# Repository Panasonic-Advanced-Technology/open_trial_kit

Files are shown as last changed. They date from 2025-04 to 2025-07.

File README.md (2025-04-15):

# @mobi open_trial_kit 1.0

@mobi Open Trial Kit 1.0は、手軽にAMR/AGVの実験や研究開発に使用できる台車として設計しました。
会社から購入しやすいようにネット通販のみで入手できる部品は極力使用していません。

組み立て方法については下記の記事をご参照ください。

[@mobi Open Trial Kit 1.0]
https://qiita.com/yamamoto-kazusige/items/2093b6a97f03b2b13532

******************************************************************************
 @mobi Open Trial Kit 1.0は、パナソニック アドバンストテクノロジー株式会社が
 配布しています。
 使用している部品メーカー様にお問い合わせなさらないようにお願いします。
******************************************************************************

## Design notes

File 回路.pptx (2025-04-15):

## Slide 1

照光スイッチ

Emg

非常停止ﾎﾞﾀﾝ

FG

24V

BLV-KRD

RS485GND 22
RS485+ 23
RS485- 24

FG

0V

Batt 12V

Batt 12V

通信電源+

20

HE
リレー

通信電源-

QSTOP

21

18

15

IN-COM

24V

BLV-KRD

RS485GND 8
RS485+ 9
RS485- 10

コントローラの
RS485へ

22
23
24

B-

B+ 24V

FG

0V

充電
ｺﾈｸﾀ

通信電源+

通信電源-

20

21

IN-COM

QSTOP

18

15

コモン端子台TNC10

DCDC
24V->12V

ｵﾑﾛﾝ端子台

FG

OUT12V

コモン端子台TNC10

IN24V

PC

20LX

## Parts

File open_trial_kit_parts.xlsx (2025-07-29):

 |  |  |  |  |  |  | 価格は 2025/7 現在のものです
 | 品名 |  | メーカー | 品番・仕様 | 数量 | 発注数 | 概算価格 | 合計
 | モーター |  |  |  |  |  |  | 142180
 |  | ブラシレスモーター | オリエンタルモーター | BLMR460SHK-GFV | 2 | 2 | 21000 | 42000 | https://www.orimvexta.co.jp/shop/item/detail/00144838/
 |  | ギヤヘッド | オリエンタルモーター | GFV4G15 | 2 | 2 | 11500 | 23000 | https://www.orimvexta.co.jp/shop/item/detail/00136830/
 |  | ドライバ | オリエンタルモーター | BLVD-KRD | 2 | 2 | 32130 | 64260 | https://www.orimvexta.co.jp/shop/item/detail/00139688/
 |  | 接続ケーブル(30cm) | オリエンタルモーター | CCM003B1ABF | 2 | 2 | 2720 | 5440 | https://www.orimvexta.co.jp/shop/item/detail/00144801/
 |  | モーター取付金具 | オリエンタルモーター | SOL4M6F | 2 | 2 | 2380 | 4760 | https://www.orimvexta.co.jp/shop/item/detail/00134044/
 |  | 電源ケーブル | オリエンタルモーター | LC03D06A | 2 | 2 | 1360 | 2720 | https://www.orimvexta.co.jp/shop/item/detail/00131331/
 | 電源系 |  |  |  |  |  |  | 38520
 |  | バッテリーパック | モノタロウ | MNX4L-BS | 2 | 2 | 2498 | 4996 | https://www.monotaro.com/p/7589/7624/?t.q=MNX4L-BS
 |  | 充電器 | メルテック | MP-230 | 1 | 1 | 14980 | 14980 | https://www.monotaro.com/p/4505/0478/?t.q=MP-230
 |  | 充電コネクタ | Neutrik | NL4FX | 1 | 1 | 2172 | 2172 | https://amzn.asia/d/9i35Aej
 |  | 充電コネクタ | Neutrik | NL4MP-ST | 1 | 1 | 1600 | 1600 | https://amzn.asia/d/6iJaPEA | https://www.mouser.jp/ProductDetail/Neutrik/NL4MP-ST?qs=erV61lVMmP8w7yPIYNaFtw%3D%3D
 |  | DCDC | MEAN WELL | DDR-60G-12 24->12V 60W | 1 | 1 | 6020 | 6020 | https://www.mouser.jp/ProductDetail/MEAN-WELL/DDR-60G-12
 |  | 電圧計 | amazon |  | 1 | 1 | 695 | 695 | https://amzn.asia/d/bLz6KK5
 |  | 非常停止ボタン | IDEC | ミスミ品番：AB6E-3BV01PRH | 1 | 1 | 1540 | 1540 | https://jp.misumi-ec.com/vona2/detail/222000391908/?PNSearch=AB6E-3BV01PRH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
 |  | パワーリレー | Panasonic | HE1AN-S-DC24V | 1 | 1 | 2720 | 2720 | https://jp.misumi-ec.com/vona2/detail/222005836525/?PNSearch=HE1AN-S-DC24V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
 |  | 低電圧保護基盤 | ---- | ---- | 1 | 1 | 1636 | 1636 | https://amzn.asia/7wLcxFT
 |  | 照光押ボタンスイッチ | IDEC | AL6H-A14PG | 1 | 1 | 1698 | 1698 | https://www.monotaro.com/p/5976/9927/
 |  | スイッチガード | IDEC | AL-KH6S | 1 | 1 | 229 | 229 | https://www.monotaro.com/p/0248/4194/
 |  | DINレール | ミスミ | DNR315-200 | 1 | 1 | 234 | 234 | https://jp.misumi-ec.com/vona2/detail/110302032560/?PNSearch=DNR315-200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
 | 端子台 |  |  |  |  |  |  | 4230
 |  | コモン端子台(4個入) | パトライト | TNC10 | 1 | 1 | 2968 | 2968 | https://jp.misumi-ec.com/vona2/detail/222005625813/?HissuCode=TNC10
 |  | 信号端子台 | オムロン | XW5T-P1.5-1.2-1 | 5 | 5 | 96 | 480 | https://www.monotaro.com/p/2440/9367/
 |  | XW5T-P用 ストッパ | オムロン | XW5Z-EP6 | 2 | 2 | 54 | 108 | https://www.monotaro.com/p/2440/9254/
 |  | ショートバー | オムロン | XW5S-P1.5-2RD | 4 | 4 | 99 | 396 | https://www.monotaro.com/p/2441/2106/
 |  | ショートバー | オムロン | XW5S-P1.5-3RD | 2 | 2 | 139 | 278 | https://www.monotaro.com/p/2441/2072/
 | コントローラー |  |  |  |  |  |  | 28944
 |  | PC | N97 MINI PC |  | 1 | 1 | 28944 | 28944 | https://amzn.asia/d/bluqHM6
 | 車輪 |  |  |  |  |  |  | 51032
 |  | 駆動輪ホイール | meviy | MVTUP-APW-456-7J5B4 | 2 | 2 | 15434 | 30868 | https://meviy.misumi-ec.com/ja-jp/
 |  | 金属ワッシャ | ミスミ | FWSSA-D30-V5.5-T4 | 2 | 2 | 510 | 1020 | https://jp.misumi-ec.com/vona2/detail/110300231910/?PNSearch=FWSSA-D30-V5.5-T4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
 |  | 駆動輪ウレタン A70 | ミスミ | AXFM-D125-L30-V85-N | 2 | 2 | 5510 | 11020 | https://jp.misumi-ec.com/vona2/detail/110300272940/?PNSearch=AXFM-D125-L30-V85-N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
 |  | センターボルト | ミスミ | HXNHFFLT-SUS-M5-12 | 2 | 2 | 36 | 72 | https://jp.misumi-ec.com/vona2/detail/221005020811/?PNSearch=HXNHFFLT-SUS-M5-12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
 |  | キャスター | シシク | 緩衝キャスター SAJ-TS6-SJ-50R | 2 | 2 | 4026 | 8052 | https://jp.misumi-ec.com/vona2/detail/221000601530/?HissuCode=SAJ-TS6-SJ-50R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
 | フレーム部材 |  |  |  |  |  |  | 74933
 |  | 底板 | meviy | MVSHM-AW05001-3WF-EFSA2 | 1 | 1 | 10832 | 10832 | https://meviy.misumi-ec.com/ja-jp/
 |  | IMU固定板 | meviy | MVSHM-AW05003-3WF-T2MRD | 1 | 1 | 5842 | 5842 | https://meviy.misumi-ec.com/ja-jp/
 |  | スイッチパネル | meviy | MVSHM-AS03002-3Y5-72S4S | 1 | 1 | 9406 | 9406 | https://meviy.misumi-ec.com/ja-jp/
 |  | コネクタスペーサー（3Dプリンタ出力もOK） | meviy | MVBLK-ABN-3Y6-E6DKS | 1 | 1 | 3268 | 3268 | https://meviy.misumi-ec.com/ja-jp/
 |  | LiDARベース | meviy | MVSHM-3N03000-456-YRTZX | 1 | 1 | 2424 | 2424 | https://meviy.misumi-ec.com/ja-jp/
 |  | PCベース | meviy | MVSHM-3N03000-3Y6-M7CMU | 1 | 1 | 2527 | 2527 | https://meviy.misumi-ec.com/ja-jp/
 |  | モータースペーサ（3Dプリンタ出力もOK) | meviy | MVBLK-ABN-3Y6-U1AJ9 | 2 | 2 | 4005 | 8010 | https://meviy.misumi-ec.com/ja-jp/
 |  | モータースペーサ（3Dプリンタ出力もOK) | meviy | MVBLK-ABN-3Y6-Y89JW | 2 | 2 | 3180 | 6360 | https://meviy.misumi-ec.com/ja-jp/
 |  | キャスター取り付けプレート | ミスミ | JSHDS-SUD-A60-B60-T2-L30-G30-N8-D12.5 | 2 | 2 | 1480 | 2960 | https://jp.misumi-ec.com/vona2/detail/110302699840/?PNSearch=JSHDS-SUD-A60-B60-T2-L30-G30-N8-D12.5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
 |  | アルミフレーム2 | ミスミ | NFS5-2080-102.5-TPW | 3 | 3 | 1941 | 5823 | https://jp.misumi-ec.com/vona2/detail/110311093859/?PNSearch=NFS5-2080-102.5-TPW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
 |  | アルミフレーム3 | ミスミ | NFSL6-3060-105-RTP | 1 | 1 | 736 | 736 | https://jp.misumi-ec.com/vona2/detail/110311094849/?PNSearch=NFSL6-3060-105-RTP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
 |  | アルミフレーム4 | ミスミ | NFS6-6060-50-TPW-CW | 2 | 2 | 2310 | 4620 | https://jp.misumi-ec.com/vona2/detail/110311095569/?PNSearch=NFS6-6060-50.5-TPW-CW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
 |  | アルミフレーム5 | ミスミ | NFSL6-3030-300 | 2 | 2 | 190 | 380 | https://jp.misumi-ec.com/vona2/detail/110311092329/?PNSearch=NFSL6-3030-300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
 |  | アルミフレーム6 | ミスミ | NFSL6-3030-172 | 2 | 2 | 178 | 356 | https://jp.misumi-ec.com/vona2/detail/110311092329/?PNSearch=NFSL6-3030-172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
 |  | フレームキャップ | ミスミ | HFC6-3030-S | 4 | 4 | 178 | 712 | https://jp.misumi-ec.com/vona2/detail/110300446540/?PNSearch=HFC6-3030-S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
 |  | 低頭六角穴ボルト M5 10mm | ミスミ | CBSA5-10 | 15 | 15 | 90 | 1350 | https://jp.misumi-ec.com/vona2/detail/110302603510/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
 |  | 低頭六角穴ボルト M8 10mm | ミスミ | CBSA8-10 | 10 | 10 | 140 | 1400 | https://jp.misumi-ec.com/vona2/detail/110302603510/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
 |  | インサート M5 M8 ピッチ1.25 | --- | １０個入り | 1 | 1 | 897 | 897 | https://amzn.asia/d/d7DC6Oo
 |  | 六角穴ボルト M3 8mm | ミスミ | CBE3-8 | 7 | 10 | 58 | 580 | https://jp.misumi-ec.com/vona2/detail/110302280360/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
 |  | 皿小ねじ M3 20mm | SUNCO | CSPCSZ-STU-M3-20 | 2 | 4 | 17 | 68 | https://jp.misumi-ec.com/vona2/detail/221000547315/?PNSearch=CSPCSZ-STU-M3-20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
 |  | 六角穴ボルト M4 15mm | ミスミ | CBE4-15 | 4 | 4 | 90 | 360 | https://jp.misumi-ec.com/vona2/detail/110302280360/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
 |  | 六角穴ボルト M5 12mm | ミスミ | CBE5-12 | 28 | 28 | 59 | 1652 | https://jp.misumi-ec.com/vona2/detail/110302280360/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
 |  | 六角穴ボルト M5 25mm | ミスミ | CBE5-25 | 8 | 10 | 59 | 590 | https://jp.misumi-ec.com/vona2/detail/110302280360/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
 |  | 六角ナット M5 | ミスミ | LBNR5 | 2 | 2 | 81 | 162 | https://jp.misumi-ec.com/vona2/detail/110300250540/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
 |  | 六角ナット M12 | ミスミ | LBNR12 | 2 | 2 | 170 | 340 | https://jp.misumi-ec.com/vona2/detail/110300250540/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
 |  | 平座金 M5 | ミスミ | PWF5 | 2 | 2 | 102 | 204 | https://jp.misumi-ec.com/vona2/detail/110300252910/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
 |  | フレームナット6シリーズM5 後入れバネナット | ミスミ | HNTP6-5 | 4 | 4 | 49 | 196 | https://jp.misumi-ec.com/vona2/detail/110302611210/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
 |  | フレームナット6シリーズM5 後入れ | ミスミ | HNTA6-5 | 33 | 33 | 40 | 1320 | https://jp.misumi-ec.com/vona2/detail/110302611120/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
 |  | フレームナット5シリーズM4 バネナット | ミスミ | HNTU5-4 | 4 | 4 | 52 | 208 | https://jp.misumi-ec.com/vona2/detail/110302608140/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
 |  | 連結ブラケット6シリーズ2穴 | ミスミ | HBLFSDK6 | 2 | 2 | 241 | 482 | https://jp.misumi-ec.com/vona2/detail/110300442950/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
 |  | 連結ブラケット5シリーズ2穴 | ミスミ | HBLFSDK5 | 2 | 2 | 230 | 460 | https://jp.misumi-ec.com/vona2/detail/110300437620/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
 |  | 連結ブラケット6シリーズ直角 | ミスミ | HBLFS6 | 6 | 6 | 68 | 408 | https://jp.misumi-ec.com/vona2/detail/110300442860/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
 | 天板（無くても良い） |  |  |  |  |  |  | 10509
 |  | アルミ天版 | meviy | MVSHM-AN05000-3Y6-ANRC2 | 1 | 1 | 7635 | 7635 | https://meviy.misumi-ec.com/ja-jp/
 |  | アルミフレーム支柱 | ミスミ | NFSL6-3030-90-RTP | 3 | 3 | 500 | 1500 | https://jp.misumi-ec.com/vona2/detail/110311092329/?PNSearch=NEFS6-3030-90-RTP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
 |  | 連結ブラケット6シリーズ直角 | ミスミ | HBLFS6 | 3 | 3 | 68 | 204 | https://jp.misumi-ec.com/vona2/detail/110300442860/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
 |  | フレームナット6シリーズM5 後入れ | ミスミ | HNTA6-5 | 6 | 6 | 40 | 240 | https://jp.misumi-ec.com/vona2/detail/110302611120/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
 |  | 六角穴ボルト M5 12mm | ミスミ | CBE5-12 | 6 | 6 | 85 | 510 | https://jp.misumi-ec.com/vona2/detail/110302280360/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
 |  | 低頭六角穴ボルト M8 10mm | ミスミ | CBSA8-10 | 3 | 3 | 140 | 420 | https://jp.misumi-ec.com/vona2/detail/110302603510/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
 | 合計 |  |  |  |  |  |  | 350348
その他調達部材(センサー例)
 | センサー
 |  | 2D LiDAR | 北陽電機 | UST-20LX | 1 | 1
 |  | IMU | WitMotion | HWT901B | 1 | 1 |  |  | https://amzn.asia/d/g8VlMhx

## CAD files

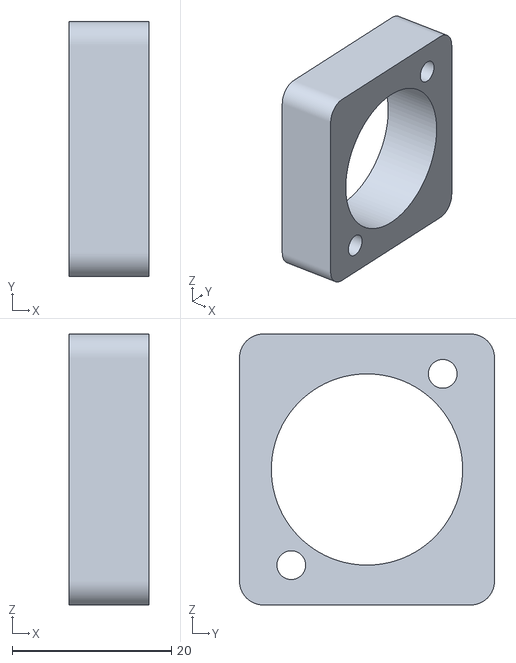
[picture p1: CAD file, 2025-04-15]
CAD/3Dプリンタ/コネクタースペーサ.stl
10.0 x 32.0 x 34.0

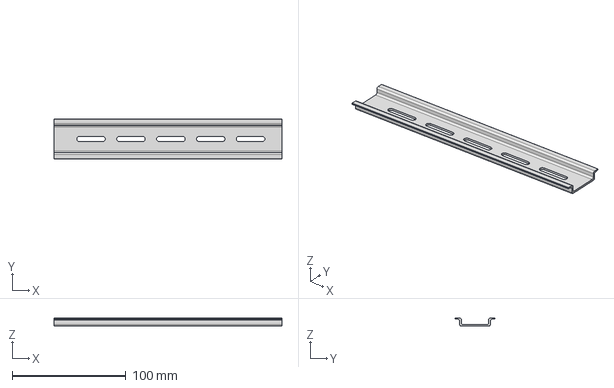
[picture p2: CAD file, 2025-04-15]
CAD/ダウンロードCADデータ/DNR274-200.stp
200.0 x 35.0 x 7.30 mm

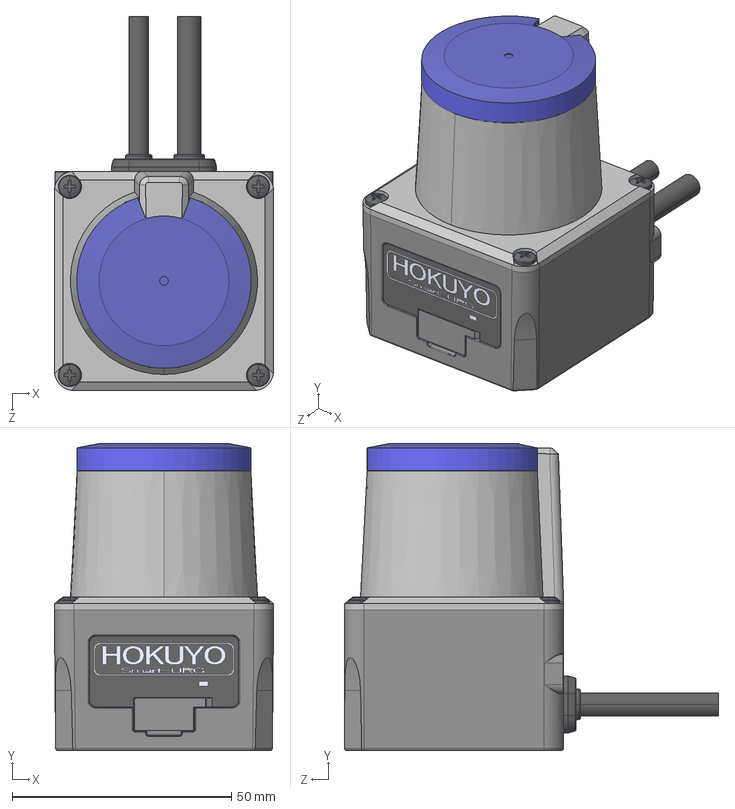
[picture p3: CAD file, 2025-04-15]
CAD/ダウンロードCADデータ/UST-10_20LX_3DCAD/UST-10_20LX.STEP
50.0 x 70.0 x 85.3 mm

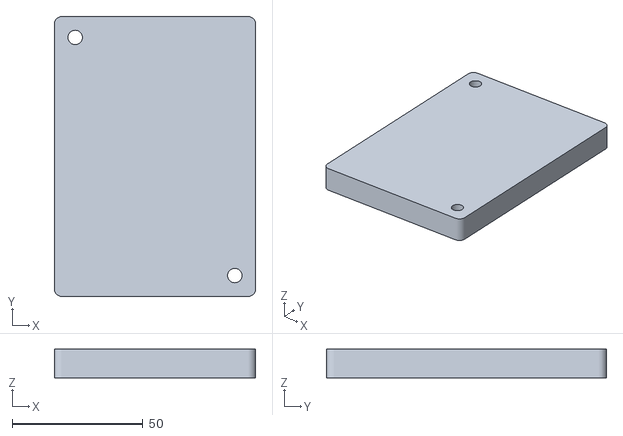
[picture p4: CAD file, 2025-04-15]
CAD/3Dプリンタ/PCベース.stl
77.0 x 107.0 x 11.0

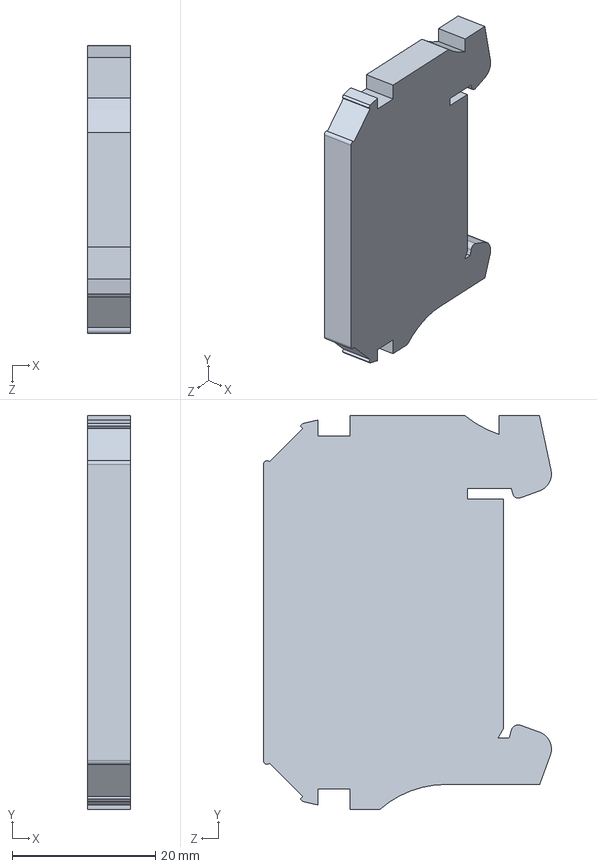
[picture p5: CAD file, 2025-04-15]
CAD/ダウンロードCADデータ/XW5Z_EP6.step
6.00 x 55.0 x 40.2 mm

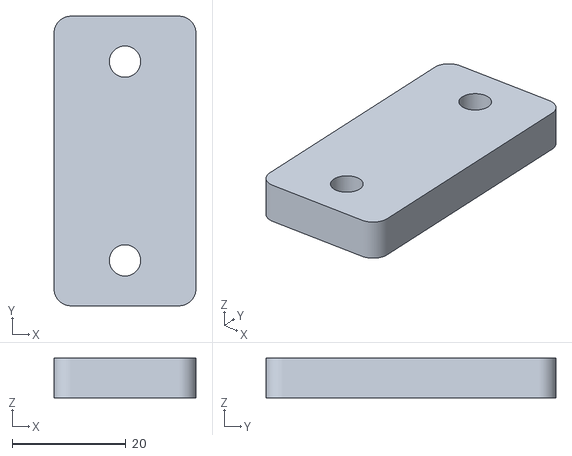
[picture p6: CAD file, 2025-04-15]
CAD/3Dプリンタ/モータースペーサー.stl
25.0 x 51.0 x 7.00

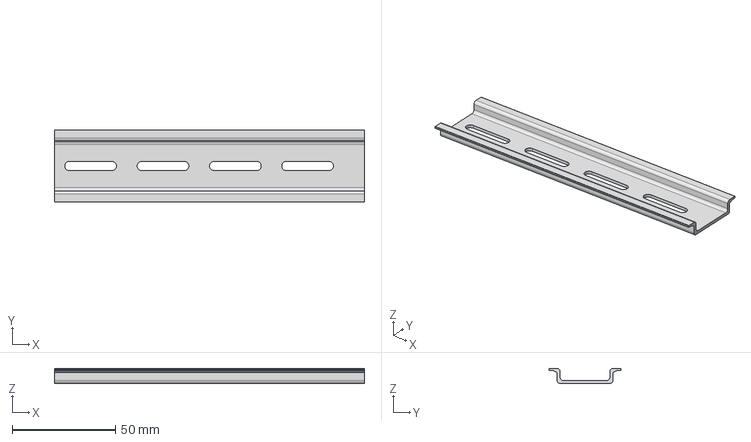
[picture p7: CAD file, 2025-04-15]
CAD/ダウンロードCADデータ/DNR274-150.stp
150.0 x 35.0 x 7.30 mm

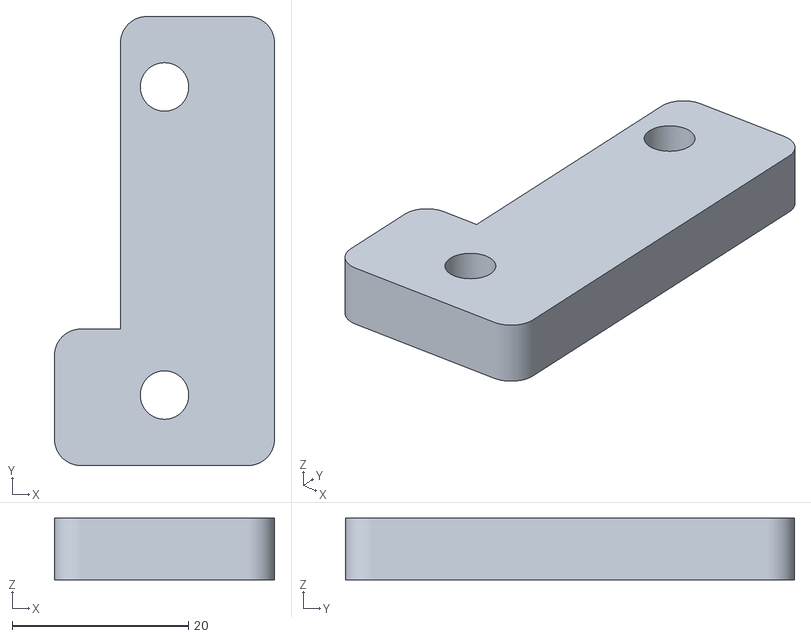
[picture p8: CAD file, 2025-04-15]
CAD/3Dプリンタ/モータースペーサー2.stl
25.0 x 51.0 x 7.00

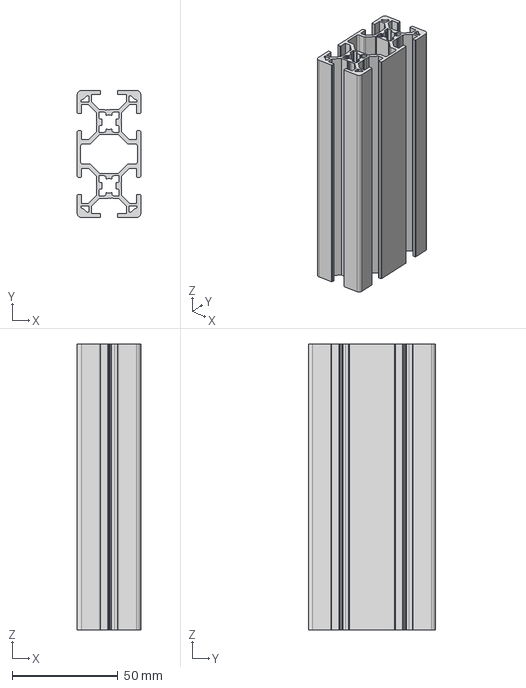
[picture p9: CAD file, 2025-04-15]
CAD/ダウンロードCADデータ/NEFS6-3060-135.stp
30.0 x 60.0 x 135.0 mm

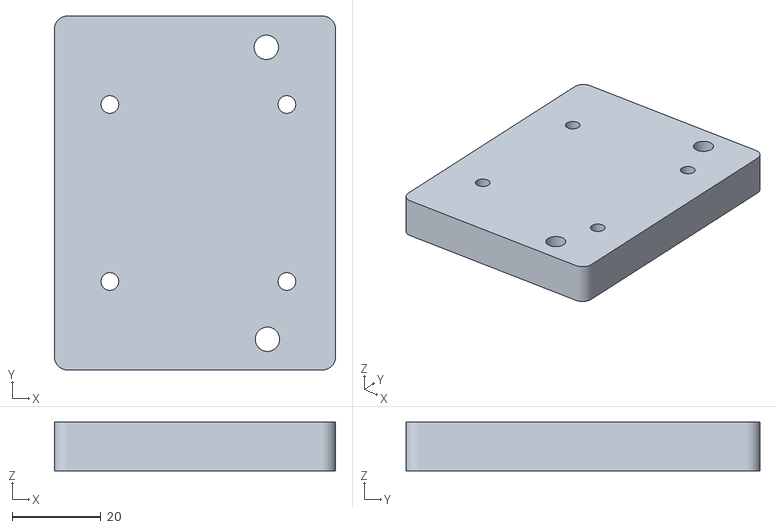
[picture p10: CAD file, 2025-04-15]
CAD/3Dプリンタ/LiDARベース.stl
63.6 x 80.0 x 11.0

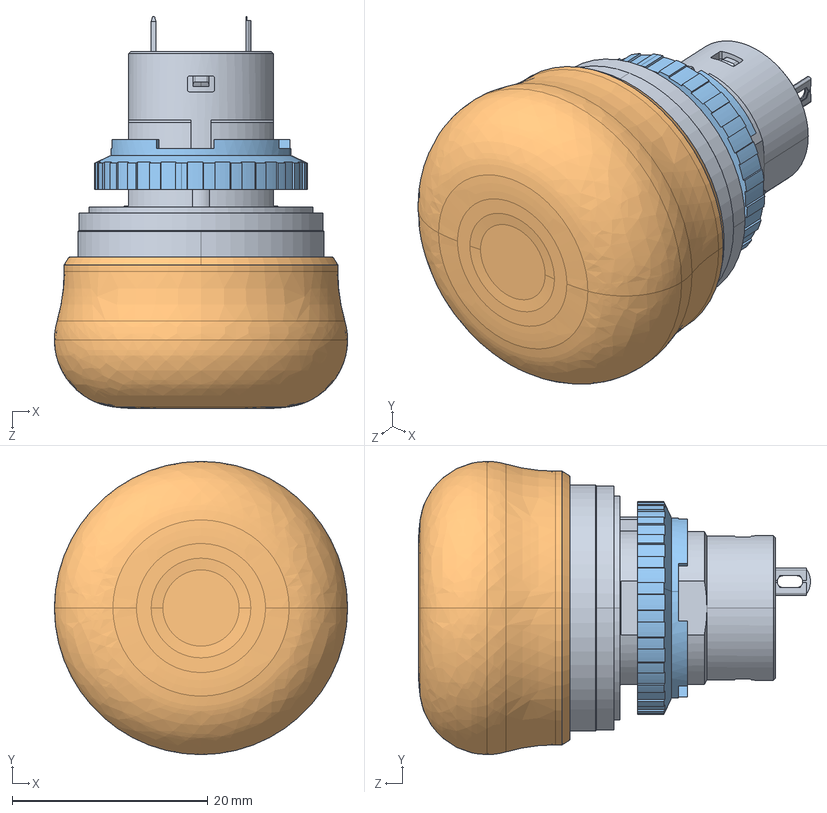
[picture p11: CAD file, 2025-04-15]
CAD/ダウンロードCADデータ/AB6E-3BV01PRH.STEP
30.0 x 30.0 x 40.1 mm
A6-BODY-V-Y_1C_蹬怮椔
A6-HANDLE-BV-RH_蹬怮椔
XA-LOCK-NUT_蹬怮椔

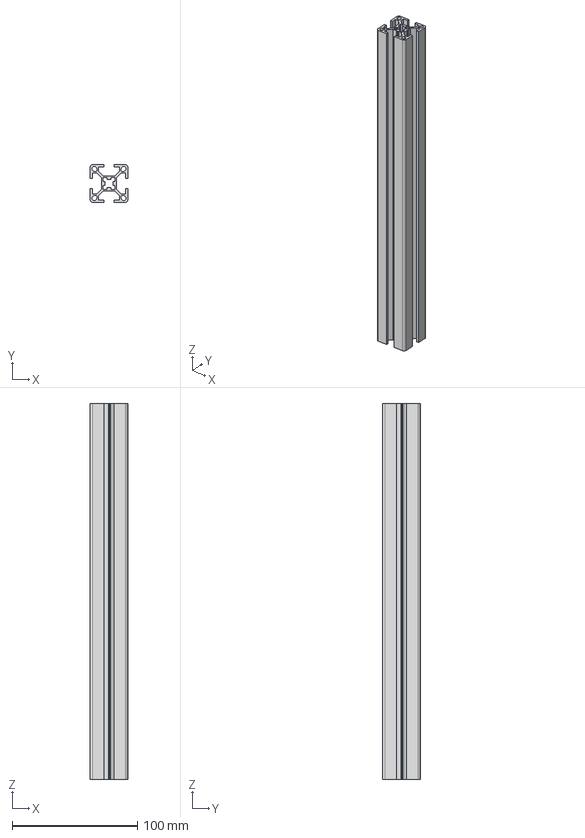
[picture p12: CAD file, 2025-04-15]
CAD/ダウンロードCADデータ/NEFS6-3030-300.stp
30.0 x 30.0 x 300.0 mm

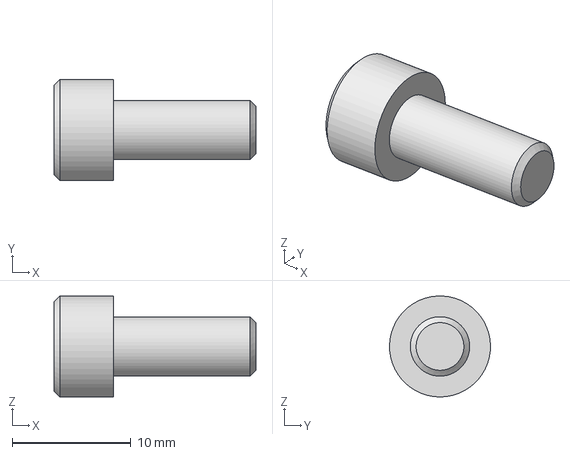
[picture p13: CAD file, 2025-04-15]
CAD/ダウンロードCADデータ/CBE5-12.stp
17.0 x 8.50 x 8.49 mm

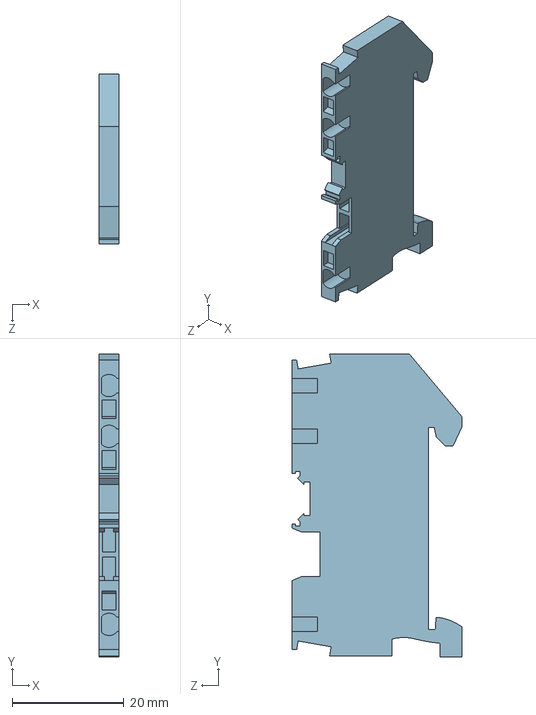
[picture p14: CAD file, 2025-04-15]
CAD/ダウンロードCADデータ/XW5T_P1_5_1_2_1BL.step
3.50 x 54.3 x 30.5 mm

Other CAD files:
CAD/ダウンロードCADデータ/SOL4M6F.stp
CAD/ダウンロードCADデータ/HBLFSDK6.stp
CAD/ダウンロードCADデータ/LBNR5.stp
CAD/ダウンロードCADデータ/rplidar-s2-model-3d.stl
CAD/ダウンロードCADデータ/AL6H-M-AL6H-A.IGS
CAD/ダウンロードCADデータ/AXFH-D125-L30-V85-N.stp
CAD/ダウンロードCADデータ/CLTUN50-R.stp
CAD/ダウンロードCADデータ/CSHELH-ST3B-M5-15.stp
CAD/ダウンロードCADデータ/DNR315-150.stp
CAD/ダウンロードCADデータ/DNR315-200.stp
CAD/ダウンロードCADデータ/HBLFS6.stp
CAD/ダウンロードCADデータ/HBLFSDK5.stp
CAD/ダウンロードCADデータ/HBLSS6.stp
CAD/ダウンロードCADデータ/HFC6-3030-S.stp
CAD/ダウンロードCADデータ/HFS6-3060-135-RTP.stp
CAD/ダウンロードCADデータ/JSHDS-SUD-A60-B60-T2-L30-G30-N8-D12.5.stp
CAD/ダウンロードCADデータ/LBNR12.stp
CAD/ダウンロードCADデータ/NEFS6-3030-172.stp
CAD/ダウンロードCADデータ/NFS5-2020-80-TPW.stp
CAD/ダウンロードCADデータ/NFS5-2080-104-TPW.stp
CAD/ダウンロードCADデータ/NFS6-6060-50.5-TPW.stp
CAD/ダウンロードCADデータ/PWF5.stp
CAD/ダウンロードCADデータ/UST-10_20LX_3DCAD/UST-10_20LX.x_t
CAD/ダウンロードCADデータ/d-nl4mp-st.stp
CAD/ダウンロードCADデータ/wl62a50.igs
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

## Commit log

2025-07-06 部品リストの間違い修正
    [open_trial_kit_parts.xlsx]
2025-07-07 部品表の価格を更新
    [open_trial_kit_parts.xlsx]
2025-07-29 メーカーの型番変更に伴う修正 ブラシレスモーターの型番変更
    [open_trial_kit_parts.xlsx]

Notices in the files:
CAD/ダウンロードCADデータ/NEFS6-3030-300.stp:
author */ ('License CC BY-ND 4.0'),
